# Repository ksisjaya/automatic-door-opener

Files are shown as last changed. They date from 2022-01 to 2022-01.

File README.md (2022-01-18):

# Summary
This project is for the course *ECE 298: Instrumentation and Prototyping*. The objective is to prototype an automatic door opener system using the [STM32F401RE MCU](https://www.st.com/en/microcontrollers-microprocessors/stm32f401re.html). Additional sensors and actuators have also been included to operate the system which is simulated in the [Proteus Design Suite](https://www.labcenter.com/). Labs go through the prototyping design process, beginning with electrical schematics and ending with Gerber plots to fabricate a PCB to host the system.

## Lab 1: Design Requirements
- Define functional, non-functional and constraint requirements
- Choose components and corresponding parameters of operation
- Define connections with the MCU and any internal MCU resources required (e.g. ADC, timers, interrupts, GPIO functions)
- Verification and validation of proper component operation, along with simulations of this
- System level block diagram

## Lab 2: MCU Interfacing
- Determine appropriate hardware interfacing with MCU pins
- Step-down voltage interfaces
- Step-up voltage interfaces
- Analog to digital interfaces
- Motor controller IC interfaces
- Simple simulations and proof-of-concept for these interfaces

## Lab 3: Prototyping
- Connecting all components with the appropriate hardware interfaces to the MCU pins
- Writing embedded software to be run on the MCU (see [Operational Overview.pdf](https://github.com/ksisjaya/automatic-door-opener/blob/main/Lab3/Operational%20Overview.pdf) for an overview of the design)
- Simulate test cases to ensure edge cases have been dealt with

## Lab 4: PCB Design
- Prepare schematics from Lab 3 to be processed into Gerber plots
- Add terminal blocks and rectangular connectors for connections
- Add decoupling capacitors
- Add nets and test points
- Generate a two layer PCB
- Route traces on the PCB
- Add vias where needed
- Generate Gerber plots
- Generate pick and place files for manufacturing
- Generate a bill of materials

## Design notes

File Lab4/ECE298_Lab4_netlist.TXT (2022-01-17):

ISIS SCHEMATIC DESCRIPTION FORMAT 8.0
=====================================
Design:   ECE298_Lab4.pdsprj
Doc. no.: <NONE>
Revision: <NONE>
Author:   <NONE>
Created:  2020-12-15
Modified: 2021-08-05

*PROPERTIES,0    

*MODELDEFS,0    

*PARTLIST,57   
C1,08056D106KAT2A,10u,CODE="Digikey 478-1417-2-ND",EID=35,PACKAGE=CAPC2012X100
C2,08056D106KAT2A,10u,CODE="Digikey 478-1417-2-ND",EID=38,PACKAGE=CAPC2012X100
C3,04022F104Z7B20D,0.1u,CODE="Digikey 311-1047-1-ND",EID=39,PACKAGE=CAPC1005X55
C4,08056D106KAT2A,10u,CODE="Digikey 478-1417-2-ND",EID=32,PACKAGE=CAPC2012X100
C5,04022F104Z7B20D,0.1u,CODE="Digikey 311-1047-1-ND",EID=24,PACKAGE=CAPC1005X55
C6,08056D106KAT2A,10u,CODE="Digikey 478-1417-2-ND",EID=4,PACKAGE=CAPC2012X100
C16,04022F104Z7B20D,0.1u,CODE="Digikey 311-1047-1-ND",EID=4B,PACKAGE=CAPC1005X55
C17,04022F104Z7B20D,0.1u,CODE="Digikey 311-1047-1-ND",EID=D,PACKAGE=CAPC1005X55
CN7,1-534236-9,1-534236-9,CODE=1-534236-9,EID=1,PACKAGE=ECE298_REVTRANS38DIL-1,SUPPLIER=TE_CONNECTIVITY
CN10,1-534236-9,1-534236-9,CODE=1-534236-9,EID=2,PACKAGE=ECE298_REVTRANS38DIL-1,SUPPLIER=TE_CONNECTIVITY
J1,CONN-SIL2,CONN-SIL2,EID=11,PACKAGE=CONN-SIL2
J2,CONN-SIL2,CONN-SIL2,EID=19,PACKAGE=CONN-SIL2
J4,CONN-SIL2,CONN-SIL2,EID=27,PACKAGE=CONN-SIL2
J5,CONN-SIL2,CONN-SIL2,EID=29,PACKAGE=CONN-SIL2
J6,CONN-SIL2,CONN-SIL2,EID=16,PACKAGE=CONN-SIL2
J7,26630301RP2,26630301RP2,CODE="NorComp 26630301RP2",EID=2D,PACKAGE=CON3_1X3_HDR_2663
J8,CONN-SIL4,CONN-SIL4,EID=B,PACKAGE=CONN-SIL4
J10,CONN-SIL7,CONN-SIL7,EID=1F,PACKAGE=CONN-SIL7
J11,CONN-SIL4,CONN-SIL4,EID=13,PACKAGE=CONN-SIL4
J12,TBLOCK-I2,TBLOCK-I2,EID=28,PACKAGE=TBLOCK-I2
J13,PIN,PIN,EID=E,PACKAGE=PIN
J14,PIN,PIN,EID=F,PACKAGE=PIN
J15,PIN,PIN,EID=1D,PACKAGE=PIN
J16,PIN,PIN,EID=22,PACKAGE=PIN
J17,CONN-SIL2,CONN-SIL2,EID=7,PACKAGE=CONN-SIL2
J18,CONN-SIL2,CONN-SIL2,EID=10,PACKAGE=CONN-SIL2
J19,CONN-SIL2,CONN-SIL2,EID=1E,PACKAGE=CONN-SIL2
J20,CONN-SIL2,CONN-SIL2,EID=23,PACKAGE=CONN-SIL2
J21,CONN-SIL2,CONN-SIL2,EID=25,PACKAGE=CONN-SIL2
J31,PIN,PIN,EID=4E,PACKAGE=PIN
J33,PIN,PIN,EID=50,PACKAGE=PIN
J38,PIN,PIN,EID=55,PACKAGE=PIN
J39,PIN,PIN,EID=56,PACKAGE=PIN
Q1,BSS138,BSS138,EID=5,PACKAGE=SOT23,SPICELIB=ZETEX,SPICEMODEL=BSS138
Q2,2N7002,2N7002,EID=2C,L=2.5E-6,PACKAGE=SOT23,SPICELIB=SUPERTEX,SPICEMODEL=2N7002,W=0.5E-2
Q3,2N7002,2N7002,EID=34,L=2.5E-6,PACKAGE=SOT23,SPICELIB=SUPERTEX,SPICEMODEL=2N7002,W=0.5E-2
Q4,2N7002,2N7002,EID=3C,L=2.5E-6,PACKAGE=SOT23,SPICELIB=SUPERTEX,SPICEMODEL=2N7002,W=0.5E-2
Q5,2N7002,2N7002,EID=12,L=2.5E-6,PACKAGE=SOT23,SPICELIB=SUPERTEX,SPICEMODEL=2N7002,W=0.5E-2
Q10,BSS138,BSS138,EID=33,PACKAGE=SOT23,SPICELIB=ZETEX,SPICEMODEL=BSS138
R1,CHIPRES10K,10k,CODE=72-0869,EID=3A,PACKAGE=0805_RES,PRIMTYPE=RESISTOR
R2,CHIPRES10K,10k,CODE=72-0869,EID=17,PACKAGE=0805_RES,PRIMTYPE=RESISTOR
R3,CHIPRES200R,200R,CODE=72-0615,EID=20,PACKAGE=0805_RES,PRIMTYPE=RESISTOR
R4,CHIPRES10K,10k,CODE=72-0869,EID=6,PACKAGE=0805_RES,PRIMTYPE=RESISTOR
R5,CHIPRES200R,200R,CODE=72-0615,EID=2E,PACKAGE=0805_RES,PRIMTYPE=RESISTOR
R6,CHIPRES200R,200R,CODE=72-0615,EID=36,PACKAGE=0805_RES,PRIMTYPE=RESISTOR
R7,CHIPRES200R,200R,CODE=72-0615,EID=3D,PACKAGE=0805_RES,PRIMTYPE=RESISTOR
R8,CHIPRES10K,10k,CODE=72-0869,EID=42,PACKAGE=0805_RES,PRIMTYPE=RESISTOR
R9,CHIPRES10K,10k,CODE=72-0869,EID=3,PACKAGE=0805_RES,PRIMTYPE=RESISTOR
R10,CHIPRES10K,10k,CODE=72-0869,EID=1B,PACKAGE=0805_RES,PRIMTYPE=RESISTOR
R11,CHIPRES10K,10k,CODE=72-0869,EID=8,PACKAGE=0805_RES,PRIMTYPE=RESISTOR
R12,CHIPRES10K,10k,CODE=72-0869,EID=3E,PACKAGE=0805_RES,PRIMTYPE=RESISTOR
R13,CHIPRES10K,10k,CODE=72-0869,EID=21,PACKAGE=0805_RES,PRIMTYPE=RESISTOR
R14,CHIPRES47K,47k,CODE=72-0949,EID=9,PACKAGE=0805_RES,PRIMTYPE=RESISTOR
R15,CHIPRES47K,47k,CODE=72-0949,EID=15,PACKAGE=0805_RES,PRIMTYPE=RESISTOR
R16,CHIPRES91K,91k,CODE=72-0973,EID=A,PACKAGE=0805_RES,PRIMTYPE=RESISTOR
R17,CHIPRES91K,91k,CODE=72-0973,EID=1A,PACKAGE=0805_RES,PRIMTYPE=RESISTOR
U10,DRV8871,DRV8871,EID=14,PACKAGE=SOIC127P600X170-9

*NETLIST,40   
NRST,2,CLASS=SIGNAL
NRST,IT
CN7,PS,14

LEDGO_OUT,3,CLASS=SIGNAL
LEDGO_OUT,LBL
Q5,PS,1
J17,PS,2

PA8,3,CLASS=SIGNAL
PA8,GT
Q5,PS,2
CN10,PS,23

PB14,3,CLASS=SIGNAL
PB14,GT
U10,IP,3
CN10,PS,28

PB13,3,CLASS=SIGNAL
PB13,GT
U10,IP,2
CN10,PS,30

MOTOR_OUT1,4,CLASS=POWER
MOTOR_OUT1,LBL
U10,OP,6
J10,PS,6
J39,PS,1

MOTOR_OUT2,4,CLASS=POWER
MOTOR_OUT2,LBL
U10,OP,8
J10,PS,7
J38,PS,1

MOTOR_ILIM,3,CLASS=POWER
MOTOR_ILIM,LBL
U10,PS,4
R1,PS,1

PA12,3,CLASS=SIGNAL
PA12,GT
J10,PS,2
CN10,PS,12

PB8,3,CLASS=SIGNAL
PB8,GT
J10,PS,3
CN10,PS,3

PB5,4,CLASS=SIGNAL
PB5,GT
R8,PS,1
J18,PS,2
CN10,PS,29

LEDGO_IN,3,CLASS=SIGNAL
LEDGO_IN,LBL
R3,PS,2
J17,PS,1

PC6,4,CLASS=SIGNAL
PC6,GT
J7,PS,2
J31,PS,1
CN10,PS,4

USI_TR,4,CLASS=SIGNAL
USI_TR,LBL
Q10,PS,1
R12,PS,2
J11,PS,3

PC11,3,CLASS=SIGNAL
PC11,GT
Q10,PS,2
CN7,PS,2

USI_ECHO,3,CLASS=SIGNAL
USI_ECHO,LBL
R15,PS,1
J11,PS,4

PB9,4,CLASS=SIGNAL
PB9,GT
R15,PS,2
R17,PS,1
CN10,PS,5

PB6,4,CLASS=SIGNAL
PB6,GT
R9,PS,1
J1,PS,2
CN10,PS,17

PB7,4,CLASS=SIGNAL
PB7,GT
R11,PS,1
J6,PS,1
CN7,PS,21

PC0,4,CLASS=SIGNAL
PC0,GT
R2,PS,1
J21,PS,2
CN7,PS,38

PC1,4,CLASS=SIGNAL
PC1,GT
R10,PS,1
J4,PS,2
CN7,PS,36

PC2,4,CLASS=SIGNAL
PC2,GT
R13,PS,1
J5,PS,2
CN7,PS,35

LEDR_OUT,3,CLASS=SIGNAL
LEDR_OUT,LBL
Q2,PS,1
J2,PS,2

PA10,3,CLASS=SIGNAL
PA10,GT
Q2,PS,2
CN10,PS,33

LEDR_IN,3,CLASS=SIGNAL
LEDR_IN,LBL
R5,PS,2
J2,PS,1

LEDY_OUT,3,CLASS=SIGNAL
LEDY_OUT,LBL
Q3,PS,1
J19,PS,2

PA11,3,CLASS=SIGNAL
PA11,GT
Q3,PS,2
CN10,PS,14

LEDY_IN,3,CLASS=SIGNAL
LEDY_IN,LBL
R6,PS,2
J19,PS,1

LEDGI_OUT,3,CLASS=SIGNAL
LEDGI_OUT,LBL
Q4,PS,1
J20,PS,2

PA9,3,CLASS=SIGNAL
PA9,GT
Q4,PS,2
CN10,PS,21

LEDGI_IN,3,CLASS=SIGNAL
LEDGI_IN,LBL
R7,PS,2
J20,PS,1

USO_TR,4,CLASS=SIGNAL
USO_TR,LBL
Q1,PS,1
R4,PS,2
J8,PS,3

PC9,3,CLASS=SIGNAL
PC9,GT
Q1,PS,2
CN10,PS,1

USO_ECHO,4,CLASS=SIGNAL
USO_ECHO,LBL
R14,PS,1
J8,PS,4
J33,PS,1

PC10,4,CLASS=SIGNAL
PC10,GT
R14,PS,2
R16,PS,1
CN7,PS,1

{NC},47
CN10,PS,2
CN10,PS,6
CN10,PS,11
CN10,PS,13
CN10,PS,15
CN10,PS,16
CN10,PS,19
CN10,PS,22
CN10,PS,24
CN10,PS,25
CN10,PS,26
CN10,PS,27
CN10,PS,34
CN7,PS,34
CN7,PS,37
CN7,PS,32
CN7,PS,30
CN7,PS,28
CN7,PS,3
J10,PS,1
CN10,PS,8
CN10,PS,7
CN10,PS,38
CN10,PS,37
CN10,PS,36
CN10,PS,35
CN10,PS,31
CN10,PS,18
CN10,PS,10
CN7,PS,9
CN7,PS,7
CN7,PS,6
CN7,PS,5
CN7,PS,4
CN7,PS,33
CN7,PS,31
CN7,PS,29
CN7,PS,27
CN7,PS,26
CN7,PS,25
CN7,PS,24
CN7,PS,23
CN7,PS,17
CN7,PS,15
CN7,PS,13
CN7,PS,11
CN7,PS,10

+3.3V,12,CLASS=POWER
+3.3V,PR
C6,PS,1
J5,PS,1
J4,PS,1
J21,PS,1
J6,PS,2
J1,PS,1
C1,PS,1
J15,PS,1
J18,PS,1
CN7,PS,16
CN7,PS,12

+5.0V,17,CLASS=POWER
+5.0V,PR
R4,PS,1
C17,PS,1
J8,PS,1
R7,PS,1
R6,PS,1
R5,PS,1
C2,PS,1
J14,PS,1
R12,PS,1
C16,PS,1
J11,PS,1
J10,PS,5
J7,PS,1
C5,PS,1
R3,PS,1
CN7,PS,18

+12.0V,6,CLASS=POWER
+12.0V,PR
J12,PS,1
C4,PS,1
J16,PS,1
U10,PP,5
C3,PS,1

GND,40,CLASS=POWER
GND,PR
C17,PS,2
Q1,PS,3
R16,PS,2
J8,PS,2
Q4,PS,3
Q3,PS,3
Q2,PS,3
R13,PS,2
R10,PS,2
R2,PS,2
R11,PS,2
R9,PS,2
C16,PS,2
C3,PS,2
Q10,PS,3
R17,PS,2
J11,PS,2
J12,PS,2
C4,PS,2
J13,PS,1
C1,PS,2
C6,PS,2
C2,PS,2
J10,PS,4
J7,PS,3
C5,PS,2
R8,PS,2
U10,PP,7
U10,PP,1
U10,PP,9
R1,PS,2
Q5,PS,3
CN10,PS,9
CN10,PS,32
CN10,PS,20
CN7,PS,8
CN7,PS,22
CN7,PS,20
CN7,PS,19

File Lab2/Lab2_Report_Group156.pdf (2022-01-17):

# Lab 2 – Feasibility Model Phase 2

ECE 298 – S2021

Lab Section: | 1215-ECE.298.041.8.LAB | Group: | 156

## DC Motor

### Summary

Item | Description
Purpose | The motor will open and close the door.
Device physical domain and range | As described in the device properties window, the motor has a zero load rotations per minute (RPM) of 360 and it runs at 24 pulses per revolution. No maximum rotations per minute is given in the device data sheet, but on testing using a 12 Volt source with a motor driver integrated circuit (IC) as shown below, the motor turns at a maximum of 176 RPM. Note that this is slightly lower than the previously tested maximum (from Lab 1) of 180 RPM, when it was directly attached to a 12 V source instead of a driver.
Device type chosen | Brushed DC Motor
Proteus Library component name | ECE298_DCMOTOR_ENCODER
Device input / output properties | The motor has two terminal inputs, in which an analog voltage is applied across. The sign (positive or negative) of the potential difference across the motor determines its direction. Note that the motor outputs (i.e. pins Q1, Q2, and IDX) are described in the 'Motor Encoder' table. Additionally, a motor driver IC (DRV8871) will be used, which accepts two digital inputs (IN1 and IN2), a 12 V source at the VM pin, and outputs an analog signal (OUT1 and OUT2) to the motor.
Device input / output range | The motor accepts voltages from 0V to 12V. Note that if accepting a pulse-width modulated (PWM) signal, the motor driver accepts a maximum logic input PWM frequency of 200 kHz (Table 6.3 of the device datasheet), while the microcontroller unit (MCU) can output a maximum PWM frequency of 42 MHz (Table 58 of the MCU datasheet). Therefore, the PWM frequency in the sub-system has a maximum of 200 kHz.
MCU connectivity details | To control the motor speed, a digital PWM output from the MCU will be required.
Device/MCU interfacing details | The MCU digital PWM output signals will be connected to the input pins (IN1 and IN2) of the DRV8871 motor driver IC. This driver will be connected to a 12 V source at the VM pin that will power the motor, thus acting as a digital to analog converter.

Lab 2 – Feasibility Model Phase 2

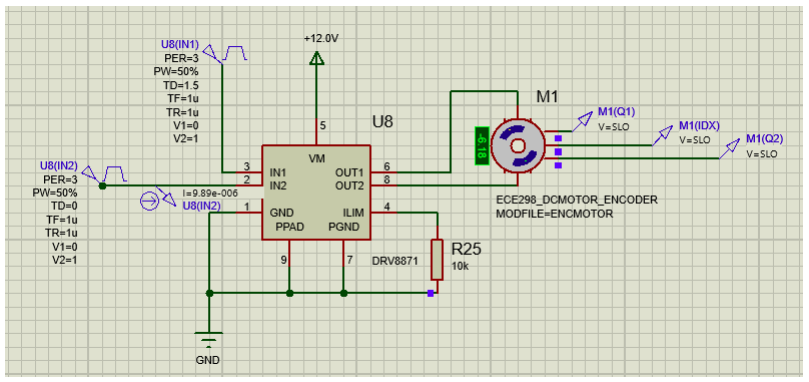
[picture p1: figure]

ECE 298 S2021Page 2 of 21

### Schematics and Simulations

Several aspects of the DC motor will be tested when driven by the interface as described above.

Figure 1 shows the schematic to test for the motor going in both directions using the motor driver interface. To simulate the outputs of the MCU digital pins, square waves with a low of 0V and high of 3.3V are outputted into IN1 and IN2. The waves have a pulse width of 50% and period of 3 seconds. It should be noted that IN1 begins at 1.5 seconds, shifting it by half a period with respect to IN2. This will simulate the MCU driving the motor to go in different directions (in this case, it will oscillate between clockwise and counterclockwise). Also note that the motor driver VM pin is connected to a 12V source; the OUT1 and OUT2 pins are connected to the motor's two terminals; the ILIM pin has a 10kOhm resistor to ground; and the PGND, PPAD and GND pins are all grounded.

Fig. 1: Motor direction testing schematic

Figure 2 shows the outputs of Q1, Q2, and IDX of the motor. The motor is set to 24 pulses per revolution, indicated by the pulses created by IDX. Likewise, as with Lab 1, the direction of the motor can be detected by the rising edges of Q1 and Q2. At 1.5 seconds, the motor is at an inflection point in turning its direction. This is reflected by the longer pulses of Q1 and Q2, indicating a slowing down of motor revolutions. After 1.5 seconds, we can see that the rising edge relationship between Q1 and Q2 has flipped, thus indicating that the motor is now rotating in the opposite direction. This pattern is repeated at 3 seconds. Thus, given this interface can drive the motor in either direction, it will be suitable.

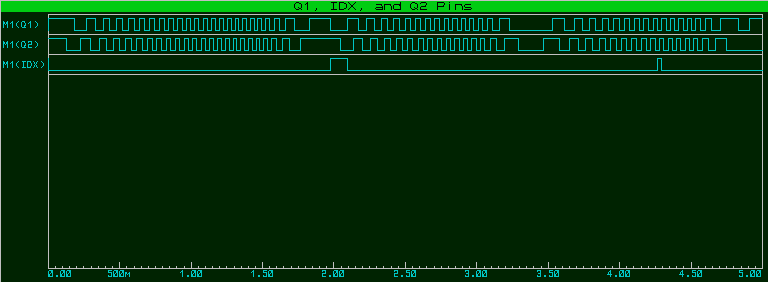
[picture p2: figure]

Fig. 2: Motor direction testing results

Figure 3 shows the schematic to test full-power in-rush current of the motor, as well as the current pulled from the MCU output at full-power. In this test, IN1 is given a constant 3.3V to represent an MCU digital output at a strong high, and IN2 is given a constant 0V to represent an MCU digital output at a strong low. Doing so provides the full extent of what the MCU can output, thus providing full power to the motor driver and therefore motor.

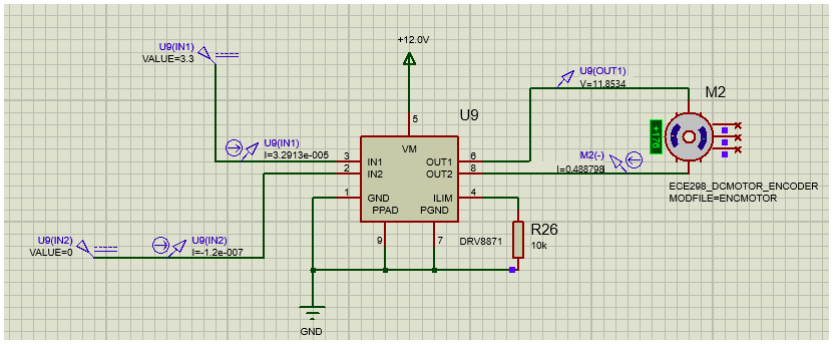
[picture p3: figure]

Fig. 3: Full power in-rush testing schematic

First, it would be useful to know if the interface draws a current within the limits of the MCU pins. Figure 4 shows the current drawn from the MCU outputs at IN1 and IN2. For U9(IN1), for which the maximum digital output from the MCU is supplied, the current remains constant at around 33µA. For U9(IN2), for which the digital output is a strong low, the current remains constant at near 0A. Therefore, the current drawn from the MCU digital output pins can be anywhere from 0A to 33µA when connected to this motor driver interface. This is much lower than the limit of 25mA per pin, making it a suitable interface.

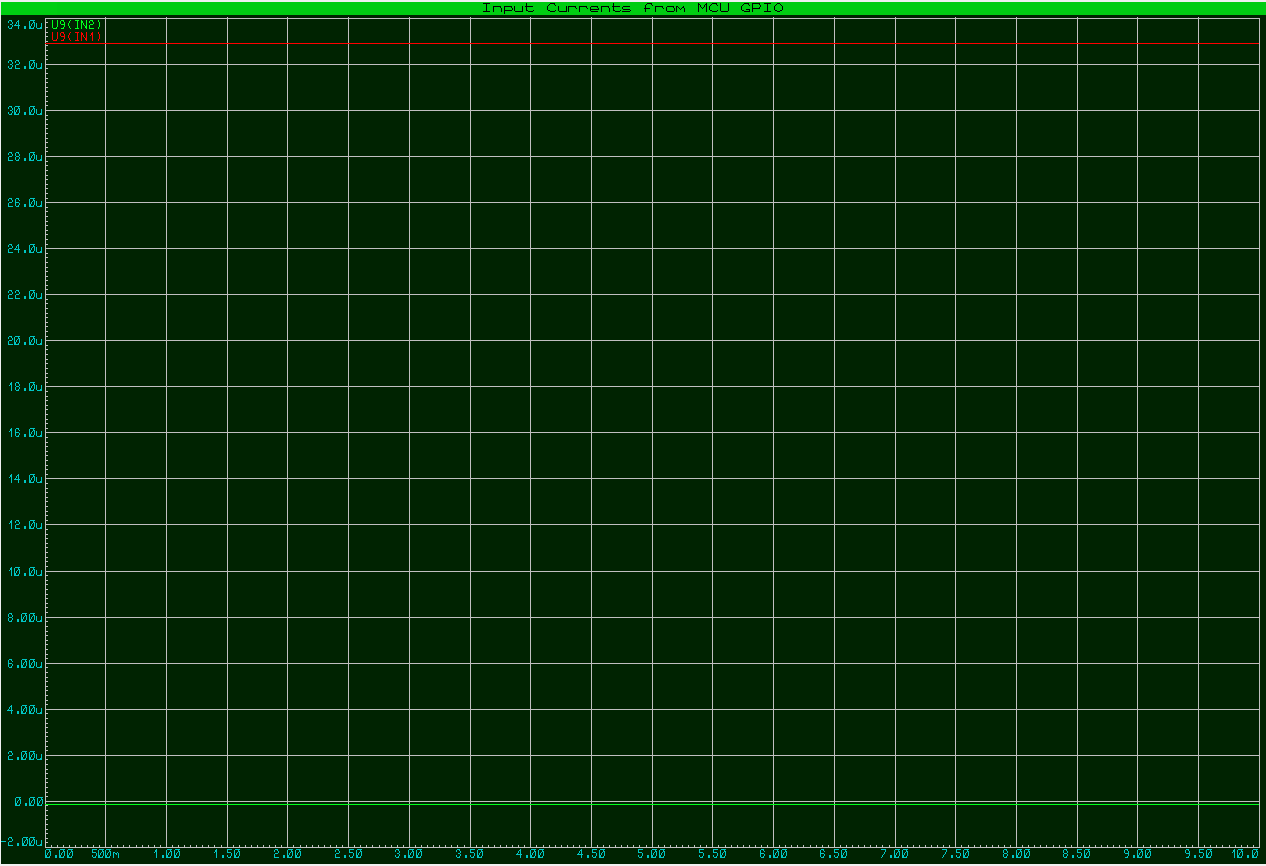
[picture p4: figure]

Fig. 4: Full power in-rush input currents to the motor driver

Figure 5 shows the full-power in-rush motor current and voltage. The voltage remains at a constant 12V, as the motor draws it from the source connected to the VM pin. The current spikes to around 952mA and stabilizes to around 500mA. Table 6.1 of the motor driver IC datasheet shows that the absolute maximum rating for the output current (at 100% duty cycle) is 3.5A. As such, the 952mA full-power in-rush current is tolerable and will not pose any major danger to damaging the IC. Therefore, this interface will be suitable in terms of handling the full power in-rush current.

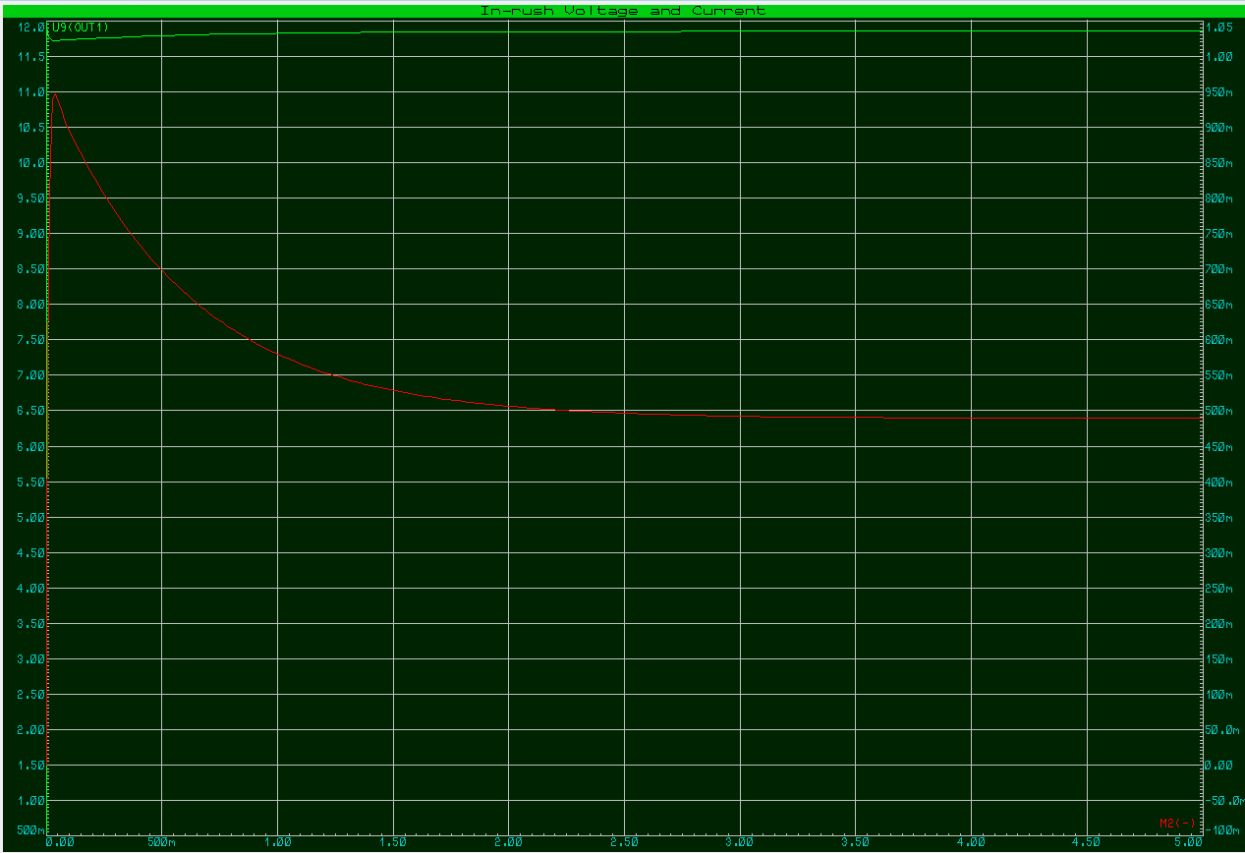
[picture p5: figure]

Fig. 5: Full power in-rush motor current and voltage

Figure 6 shows the schematic to test the motor voltage and current at varying inputs. As with the previous test, IN2 is set to 0V. However, this test sets IN1 to varying inputs of voltages (0V, 1V, 2V, 3V) to see what the interface response would be if the MCU pin output a weak high or weak low. Note that the IN1 voltages go from 0V to 3V and then down to 0V again. This is to test what the IC response would be in both directions.

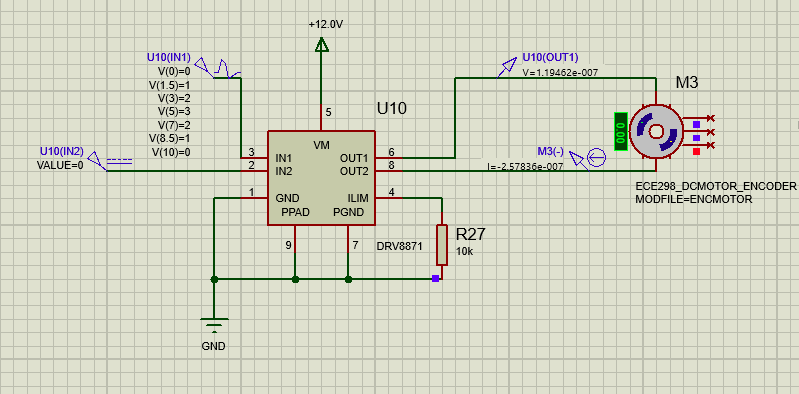
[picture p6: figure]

Fig. 6: Motor voltage and current testing schematic

Figure 7 shows the voltage and current of the motor. The voltages across the motor respond in a step-like manner, where it jumps from one value to the next. This is because the motor is no longer attached directly to the input, but rather it is being sourced by the 12V at VM. IN1 and IN2 only determines the response of the H-bridge as shown in section 7.2 of the device datasheet, which in turn determines the voltage supplied to the motor. One can see that the voltage at its maximum reaches 12V. With every step up of voltage, the current responds as though it is an in-rush current, shooting upwards and then decaying. With every step down of voltage, the current responds as though it is an out-rush current, shooting downwards and then exponentially growing. These are determined by the time constants made up of the internal resistance of the motor and any parasitic capacitances that exist. Again, the peak current only reaches around 800mA, which is far below the motor’s maximum limit (3.5A) as described in Table 6.1 of the datasheet. Therefore, the performance of this interface is within limits and is suitable.

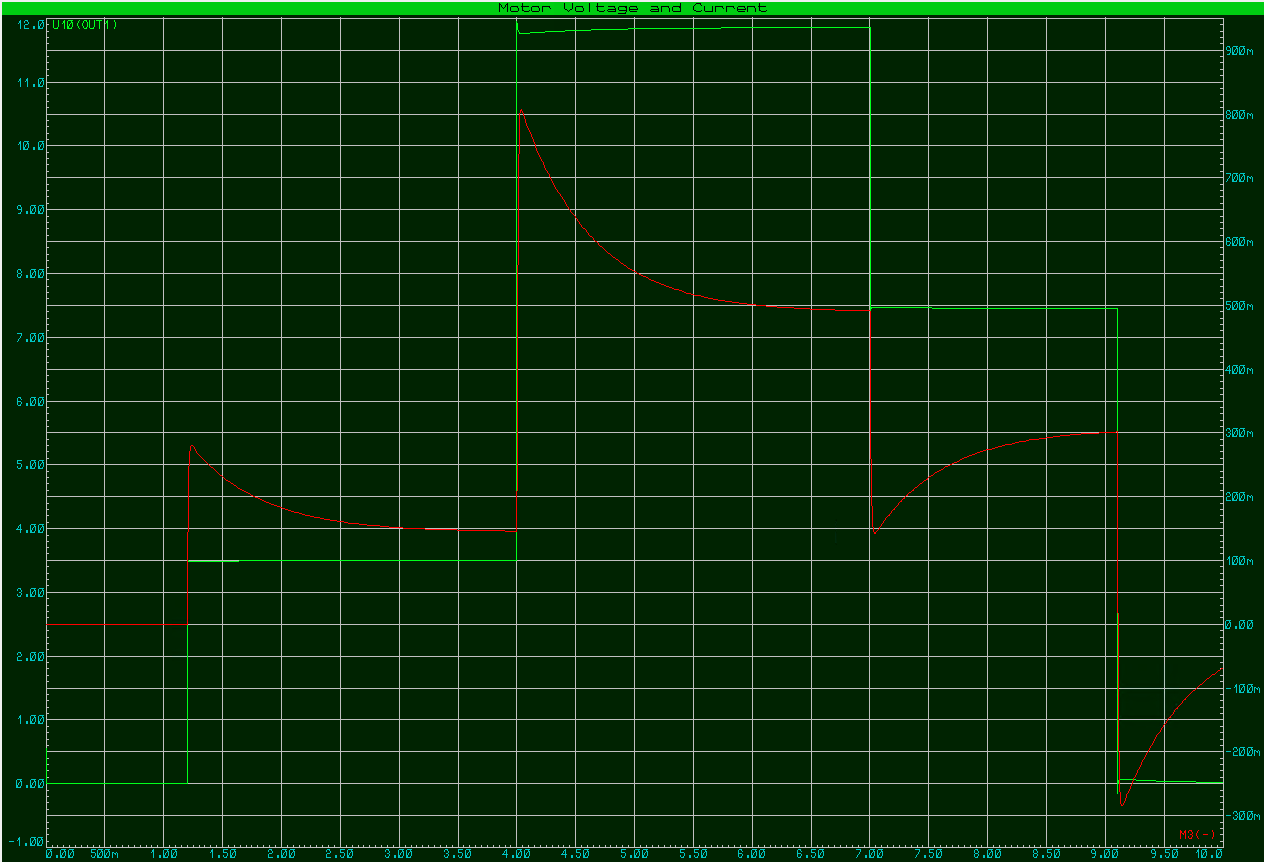
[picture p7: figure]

Fig. 7: Motor voltage and current testing results (note: y-axis scales for voltage and current do not align)

Figure 8 shows the schematic to test the motor interface under a PWM input. The PWM input is given by the PWM_input_testing.txt file which has a PWM signal with a low of 0V and high of 3.3V. As described in the device datasheet, the motor driver can take in a PWM input through IN1 and IN2, and the driver will be able to output another PWM signal to the motor. For this test, IN2 was set to 0V and IN1 had the PWM input. This corresponds to the description in the data sheet on how to use the motor driver to drive a PWM signal to the motor.

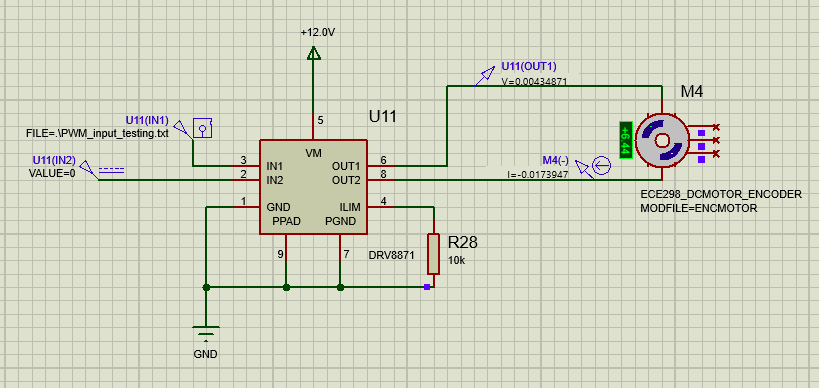
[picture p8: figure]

Fig. 8: PWM input testing schematic

Figure 9 shows the current and voltage across the motor as the PWM signal is being input. The voltage oscillates between 0V and 12V, as is expected (given that the VM pin is connected to a 12V source), and the current responds as an in-rush current, shooting up then decaying. During the PWM signal with a higher frequency, the current shoots up and down in several 'steps'. The rather quick time constant means that the current decays very quickly, resulting in larger oscillations. This can be seen by the first 'step' of current from 500ms to 700ms, where the current fluctuates between 200mA to 500mA. It should be noted that 7.4.1 and 7.4.2 of the device datasheet indicates that the motor driver can operate a PWM signal with or without current regulation. As such, it would be possible to be safer and more precise in terms of current behavior. Also note that Table 6.3 of the datasheet shows the maximum PWM frequency to be 200kHz. This is the bottleneck if also considering the MCU's maximum PWM frequency of 42 MHz. Either way, the RPM measurements of the PWM signal from the text file (which has a frequency much less than 200kHz) is high enough to provide for our needs. As such, this interface will be suitable with a PWM input. We just need to decide the proper duty cycles and frequencies of the PWM signal for our purposes.

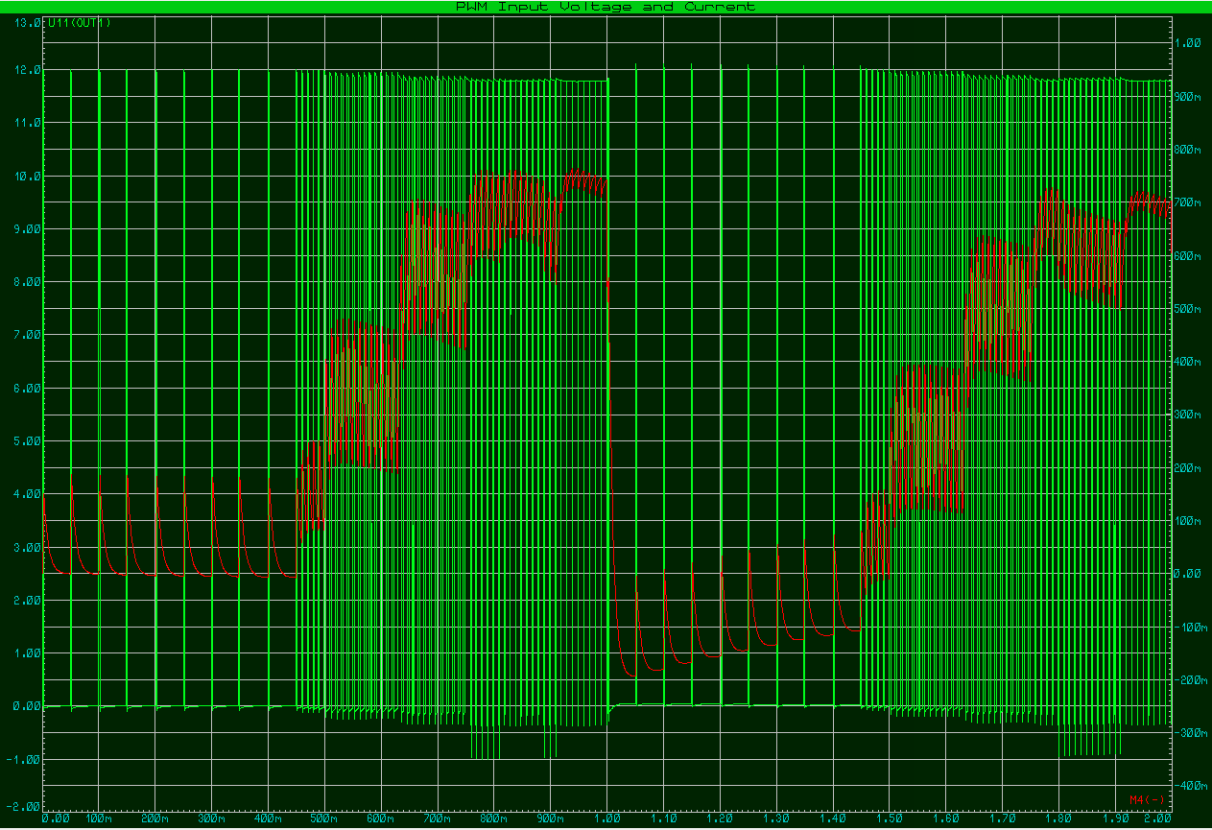
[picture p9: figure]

Fig. 9: PWM input testing results

## Light Emitting Diode (LED)

### Summary

Item | Description
Purpose | To indicate to the user the current state of the automatic door system. A red LED indicates the door in motion, a yellow LED indicates the door has collided with an object, and a green LED indicates an object is within the inside and outside proximity ranges.
Device physical domain and range | The light intensity of the LED (determined when the specific LED is chosen later) and the color of the LED (green, red, and yellow).
Device type chosen | LED
Proteus Library component name | LED-RED, LED-GREEN, LED-YELLOW
Device input / output properties | The LED has two terminals, which when an analog is applied across, will produce a current, lighting the LED. For all three components, the forward voltage at 20 mA is 2.2 V, the full drive current is 10 mA, and the minimum on-time to light the LED is 10ms.
Device input / output range | The breakdown voltage of the LEDs is 4 V, meaning that there should not be a voltage applied in the reverse direction of the diode more than 4 V. Otherwise, the LED will be damaged.

MCU connectivity details | The MCU will output a digital signal through the correct pin that is connected to the corresponding LED. Note that it is assumed that only one LED color can be turned on at a time.
Device/MCU interfacing details | The MCU pin will output a digital signal to the gate terminal of an n-channel MOSFET (2N7002). The MOSFET will act as a switch for the LED, which is connected via the drain terminal to a 5 V analog source with a pull-up resistor of 145 Ohms. The source terminal will be grounded. A digital high signal (3.3 V) applied by the MCU digital output is enough to allow current to 'turn on' the transistor, resulting in an analog input into the LED. As such, the interface acts as a digital to analog converter.

### Schematics and Simulations

Figure 10 shows the schematic for LED testing. To simulate an MCU digital output, a square wave with a low of 0V and high of 3.3V are outputted into the gate terminal of the n-channel MOSFET. The wave has a frequency of 0.5Hz, and a pulse-width of 50%. The LED is attached to the drain terminal of the MOSFET with a pull-up resistor (145 Ohm) and 5V source, and the source terminal of the MOSFET is grounded. Note that the square waves begin at 0s, 0.3s, and 0.6s for the green, red, and yellow LEDs respectively. This is to make the current measurement easier to read. But also note, that this would mean the LEDs do not turn on at the same time in the simulation.

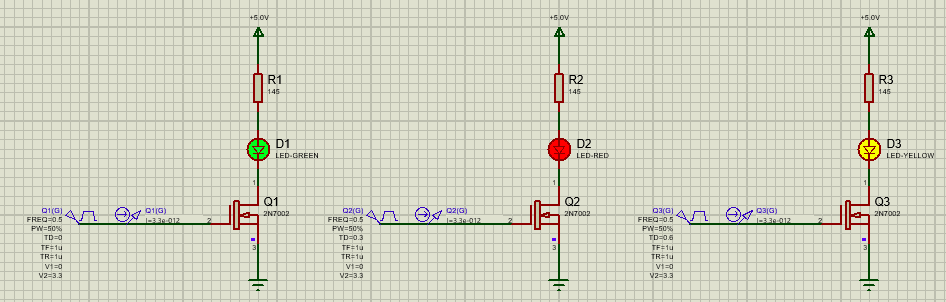
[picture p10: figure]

Fig. 10: LED interface testing schematic

Figure 11 shows the currents being drawn from the MCU pins into the interface. The maximum current being pulled from any of the three LEDs at Q1, Q2, and Q3 respectively, is around 560µA. Likewise, the minimum current being pulled from any of the three LEDS does not go below -250µA. As such, the range of operation for this interface is from -250µA to 560µA. This is far lower than the limit given in the MCU datasheet of +/-25mA per pin. Given there are 4 total LEDs in this project, the worst-case scenario would give an aggregate current of 2.24mA (i.e. all LEDs are on), which is far lower than the aggregate limit of 120mA. Also, most importantly, the LEDs turn on when the signal is high, and off when the signal is low. As such, given all these considerations, this interface will be suitable.

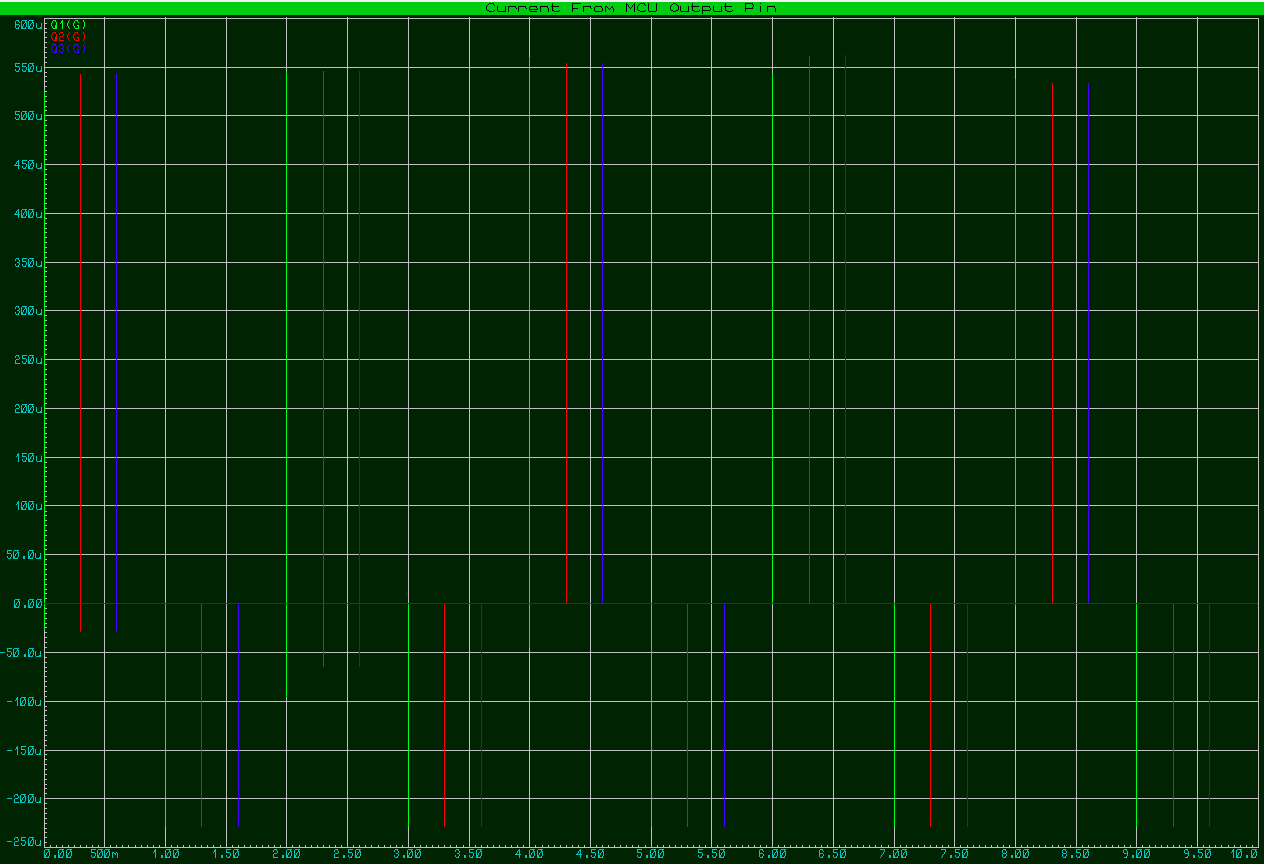
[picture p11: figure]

Fig. 11: LED interface testing results

## Liquid Crystal Display (LCD)

### Summary

Item | Description
Purpose | The LCD displays an alphanumeric string indicating the current mode of operation of the door.
Device physical domain and range | The alphanumeric string to be output to the LCD.
Device type chosen | LCD
Proteus Library component name | LM016L
Device input / output properties | The LCD has eight parallel data bus lines (D0 to D7) that correspond to the byte mapping of the ASCII characters to output. There is also an enable signal pin (E), a read-write pin (R/W), a register selector pin (RS), and the power supply pins (VDD, VSS, VEE).
Device input / output range | The LCD takes +5V digital inputs at 1 to 10 mA (section II.A of the device datasheet). The datasheet in Proteus does not show a minimum input high or a maximum input low, but the Hitachi datasheet (found online) shows a minimum input high voltage of 2.2 V and maximum input low voltage of 0.6 V (Hitachi). (https://datasheetspdf.com/pdf-file/1462370/Hitachi/LM016L/1)

MCU connectivity details | The MCU will output digital signals for the following pins on the LCD: enable (E), register select (RS), read/write (R/W), data (for now it is D7 to D4, but in the future this may include all eight pins).
Device/MCU interfacing details | The MCU digital output will be 3.3V, while the LCD accepts only 5V digital inputs. As such, a digital-to-digital unidirectional step- up voltage interface will be used to bring up the voltage to 5V. This involves inputting the MCU signal into the gate of an n- channel MOSFET, with the source grounded, and the drain connected to a pull-up resistor of 100kOhm with a 5V source. The output will be taken from the drain. But this output will be inverted. As such, an extra inverter is added to re-invert the signal to match the input signal. This step-up voltage interface will be implemented for each LCD pin being used (E, RS, RW, Data pins)..

### Schematics and Simulations

Figure 11 shows the schematic for testing the LCD using the interface. It should be noted that a pattern generator was used. However, this pattern generator only output 5V digital signals. As such, that output first needed to be stepped down to 3.3V to mimic the digital outputs coming from the MCU pins. This circuitry is shown in Figure 12, where all the needed pins from the pattern generator are pulled down using a voltage divider with two resistors of 47kOhm and 91kOhm. The pattern generator and the step down digital to digital voltage dividers can be thought of as the MCU internals, which would then output the appropriate 3.3V digital signals to the external interface, shown in Figure 13. The LCD also takes in only 5V digital signals. As such, the 3.3V outputs from the MCU need to be stepped-up using an n-channel MOSFET with a pull up resistor of 100kOhm and a 5V source. The MCU output is connected to the gate of the MOSFET, the pull up resistor to the drain, and ground to the source. However, this stepped-up voltage will be inverted due to the n-channel MOSFET. So, an extra inverter is required to re-invert the output signal, so it matches the input signal. Note that the E, R/W, and RS pins are connected, alongside the data bus line (which for now are just D7 to D4). As with Lab 1, the pattern is set to output the team number '156'.

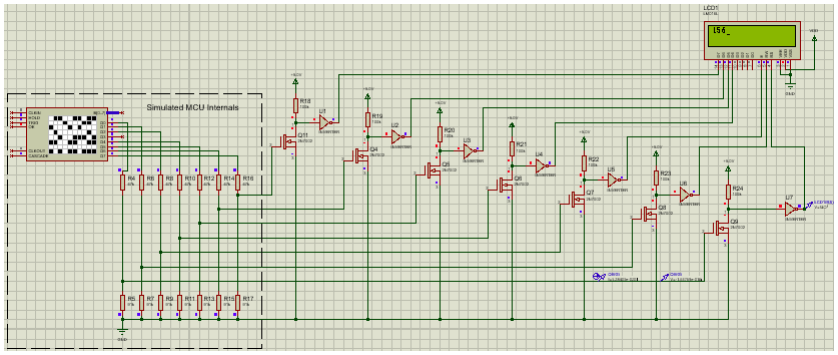
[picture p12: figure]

Fig. 11: LCD interface testing schematic

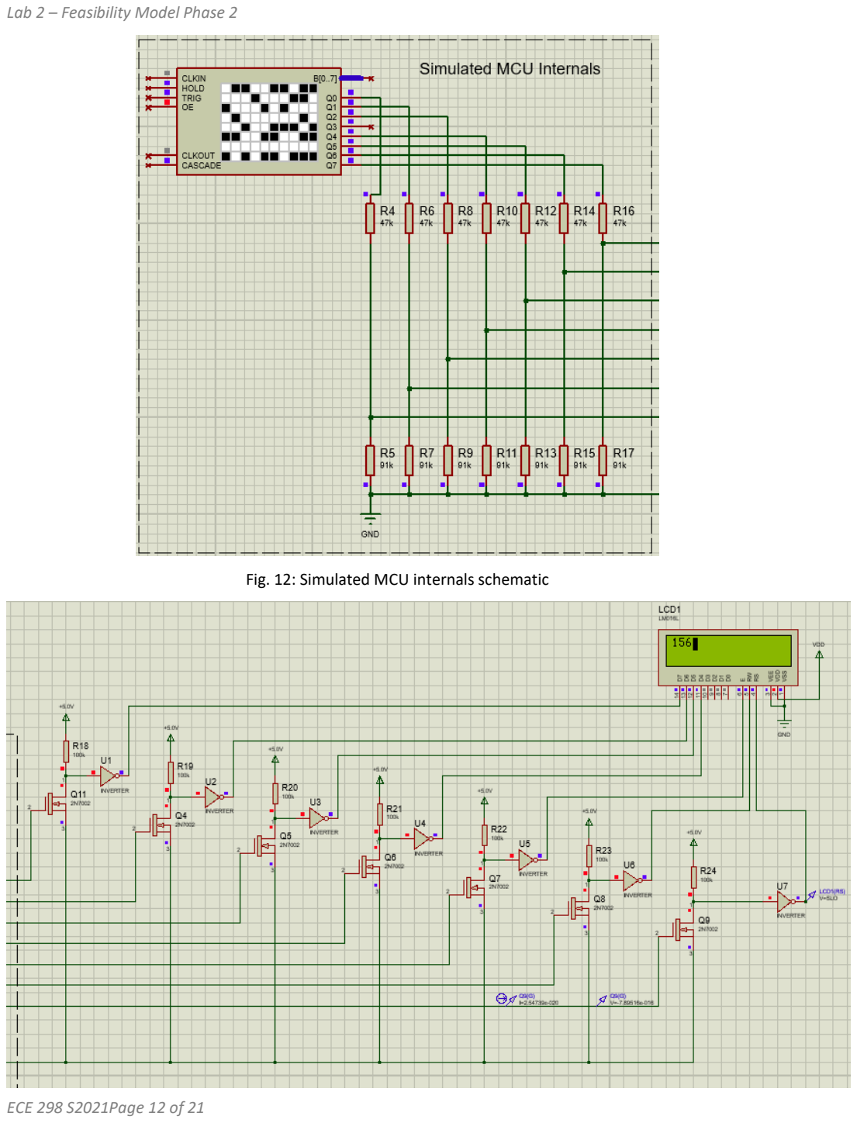
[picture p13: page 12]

Fig. 12: Simulated MCU internals schematic

Fig. 13: LCD external interface schematic

Figure 14 shows the input current, input voltage at Q9 (i.e. one of the MCU digital outputs). The figure also includes the output of the interface at LCD1(RS). First, the input current to the interface reaches a maximum of around 110µA (at 4.5 seconds), and a minimum of around -110µA (at 8.5 seconds). These current spikes coincide with transitions from a strong low to a strong high and vice versa. Either way, this tells us that the interface will draw a range of current from -110µA to 110µA, which is far below the stated MCU limit per pin of +/- 25mA. Assuming that all LCD pins are being outputted to at the same time, the aggregate current drawn from the MCU pins will be 110µA x 11, which is 1.21mA. This is also far below the stated aggregate limit on the MCU pins of 120mA. Therefore, this interface will be appropriate for the current limits. Also, it can be seen that as the input voltage is a strong low (i.e. 0V), so is the output voltage. When the input voltage Q9(G) is a strong high (3.3V from the MCU), the output voltage LCD1(RS) is a strong high of 5V for the LCD. This indicates that the step-up interface works, and this is further shown by the LCD correctly displaying '156'. Therefore, this interface will be suitable.

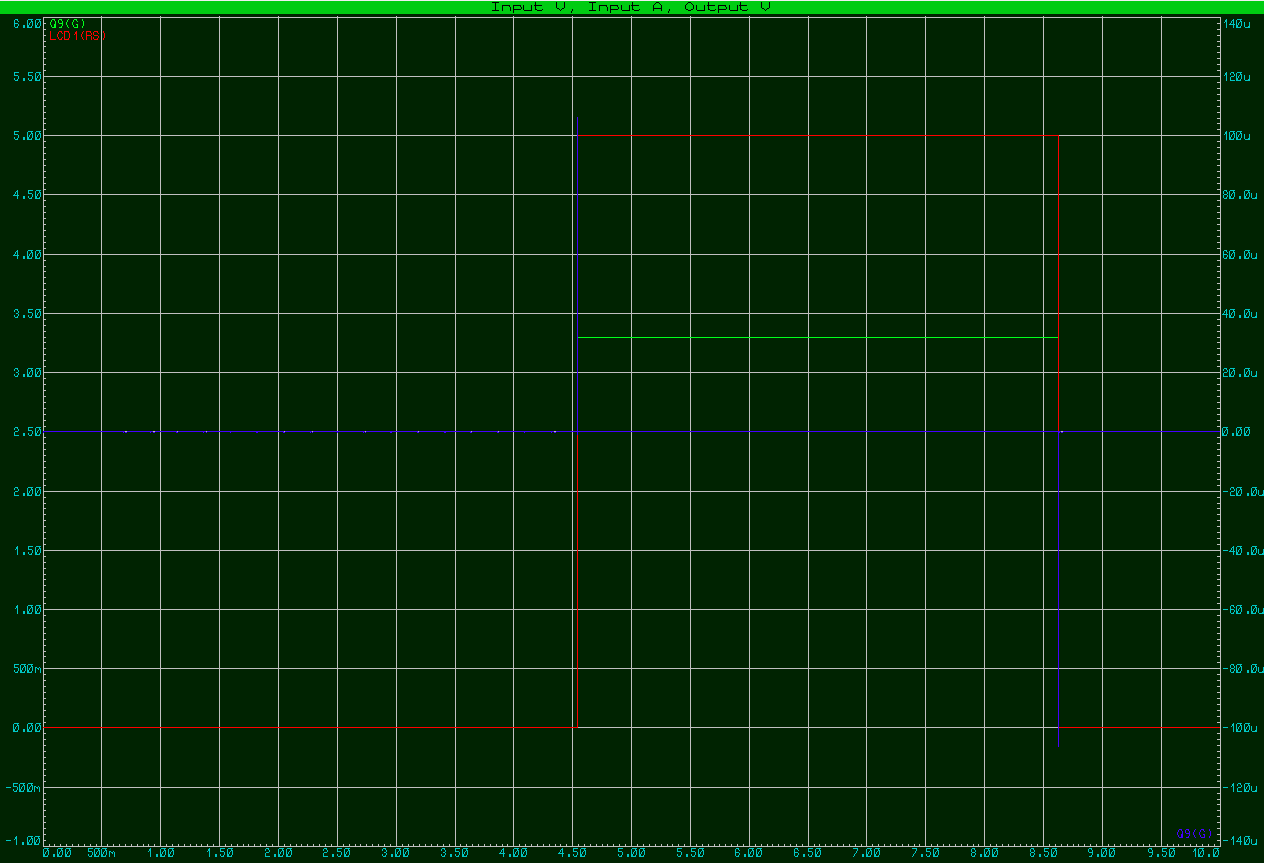
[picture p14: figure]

Fig. 14: LCD interface testing results

## Ultrasonic Ranger Module

### Summary

Item | Description
Purpose | Detects when an object is within a certain distance of the sensor so the door can automatically open.
Device physical domain and range | The module senses objects within 2cm to 4m in a range of 15 degrees.
Device type chosen | The chosen sensor is an ultrasonic proximity sensor
Proteus Library component name | HCSR04
Device input / output properties | The device has four digital input/output pins. One for source voltage and ground. The other two correspond to the input trigger TTL pulse and the time-varying echo pulse (depends time taken by pulse to leave and return). The input and output are push-pull since they can only be two values, strong 0 or strong 1.
Device input / output range | The device has a working voltage of 5V. VOH, min = 2.7V. VOL, max = 0.4V. VIH, max = 2V. VIL, min = 0.8V. The input trigger pulse must have a width of 10us and cannot be transmitted again until the echo has returned or timed out (60ms). The output signal will have a 8* 25us delay since it must wait for the sonic burst to output from the module. The output signal corresponds to the distance measured to an object and could range from around 150 us to 25ms or up to 38ms if nothing is detected.
MCU connectivity details | A digital input pin and a digital output pin will be needed for the trigger and echo pins.
Device/MCU interfacing details | Input: (D/D) The input will need an N-channel MOSFET with a pullup up resistor with an inverted signal to increase the signal. Output: (D/D) The output will need a voltage divider to scale down the signal.

### Schematics and Simulations

Figure 15 shows the schematic for testing MCU input and output to the ultrasonic ranger module. The Q1 signal generator simulates the MCU output and the Pi terminal represents the input to the MCU. Since the N-channel MOSFET inverts the signal, Q1 must start at a constant high signal of 3.3V and generate a 10us pulse of 0V. In Figure 16, you can see that’s what it does and the MOSFET correctly inverts and adjusts the signal to a 5V pulse of 10us into the trigger.

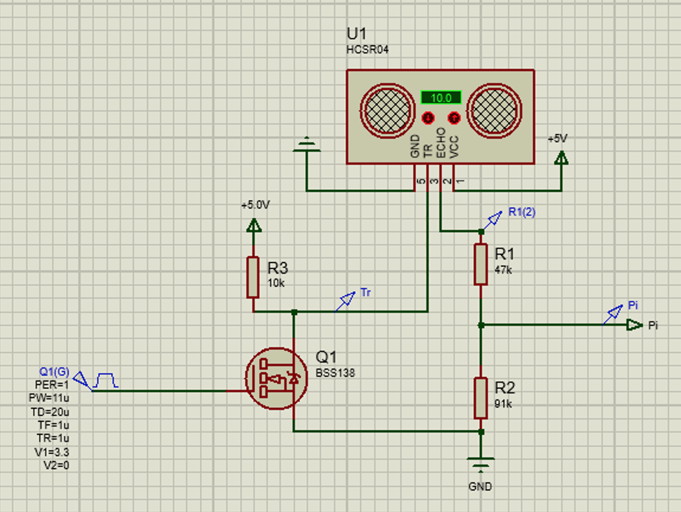
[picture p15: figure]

Fig. 15: Ultrasonic Ranger Module Interface Circuit

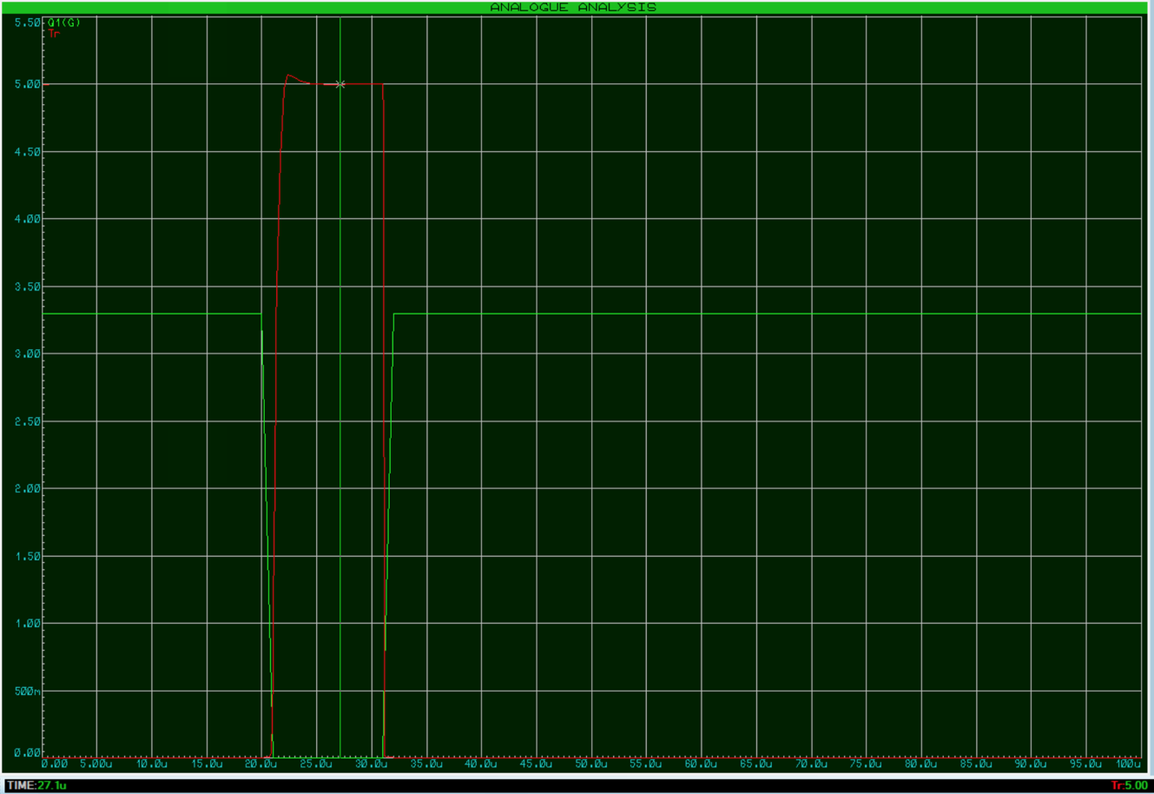
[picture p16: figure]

Fig. 16: Analog Analysis of the simulated MCU output (Q1) and the adjusted trigger input (Tr).

In Figure 17, the voltages on the ECHO line of the ranger are shown in the analog analysis as well. The signal produced straight out of the ranger module gives a varying pulse of 5V. The duration of the pulse depends on the distance of the object sensed and is not currently relevant. After adding a voltage divider, the signal is correctly reduced to 3.3 V without any change other than the magnitude, asserting that the MCU will obtain an accurate reading of the device.

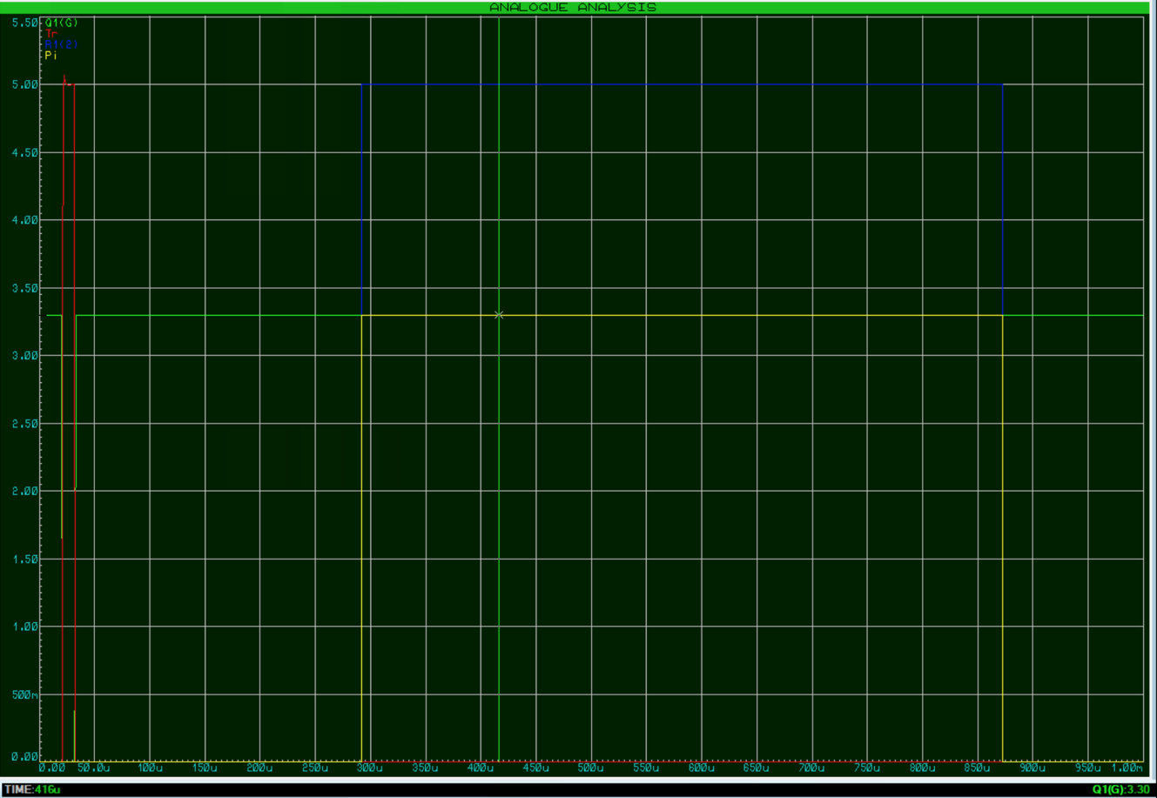
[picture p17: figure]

Fig. 17: Analog Analysis of all the voltages

## DC Motor Encoder

### Summary

Item | Description
Purpose | Senses and monitors speed and rotational direction of the door motor.
Device physical domain and range | The encoder will detect up to the motor’s maximum speed and whether it is turning clockwise or anticlockwise
Device type chosen | A position encoder attached to the shaft of a DC motor.
Proteus Library component name | ECE298_DCMOTOR_ENCODER
Device input / output properties | The encoder outputs three digital signals that are all push-pull. Two outputs must be read together to determine the rotational direction and speed of the motor. The third signal generated can also be read to determine the speed of the motor. The frequencies of the signals depend on the speed of the motor.
Device input / output range | The device has a working voltage of 5V. VOH, min = 2.7V. VOL, max = 0.4 V.
MCU connectivity details | Three digital input pins will be needed to read the signals of the encoder.
Device/MCU interfacing details | Output: (D/D), The outputs will need voltage dividers to scale down the signal.

### Schematics and Simulations

Figure 18 shows the schematic for testing the DC motor encoder. The probes labelled R7(2), R8(1), and R6(2) represents the input pins into the MCU. Since the max voltage of the output from the encoder is greater than what is accepted into the MCU, three voltage dividers will be needed to reduce the signal. A generic 1V DC generator is inputted into the motor to run it, since the encoder depends on the motor to work.

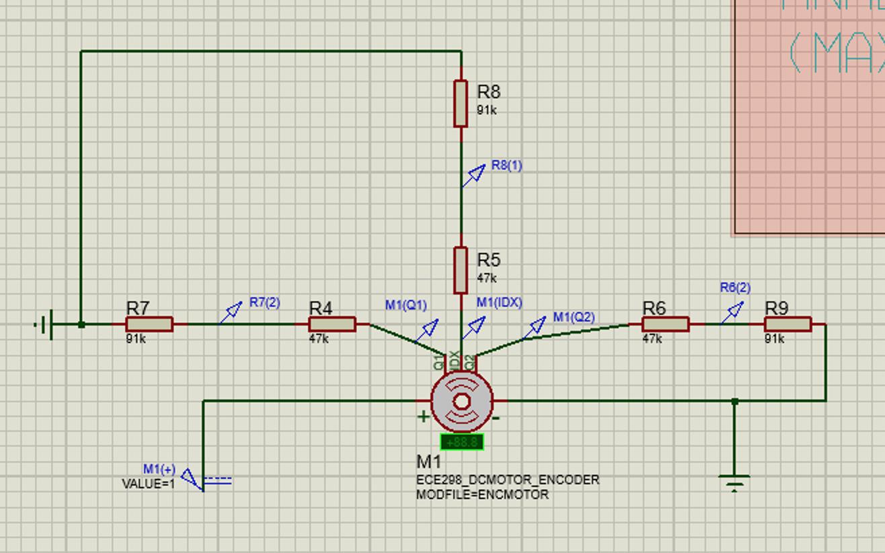
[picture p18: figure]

Fig. 18: DC Motor Encoder Interface Circuit

Figure 19 shows the three outputs of the encoder. All three signals have a high of 5V which is too high for the MCU to read. The pulses of the signal are dependent on the rotational speed and direction of the motor and are not relevant currently. Using digital analysis they can be more accurately read and deciphered but that is not necessary for only interfacing testing with the MCU.

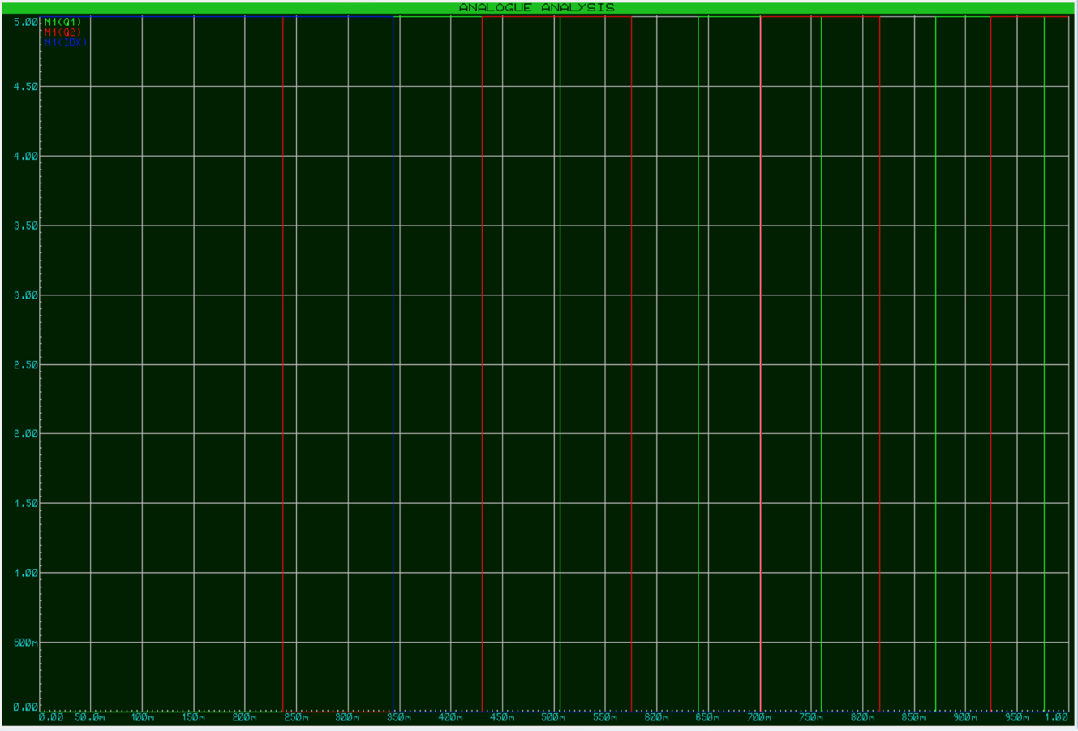
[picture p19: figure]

Fig. 19: Analog Analysis of the Outputs of the Encoder

In figure 20, the analog analysis shows the readings of the probes, simulating the signal into the MCU. The signal has been reduced to 3.3V which is what we need. Also, when comparing with Figure 19, there is no difference between the output of the encoder and the input into the MCU other than the magnitude of the signal which is important since we need to preserve the information transmitted by the encoder.

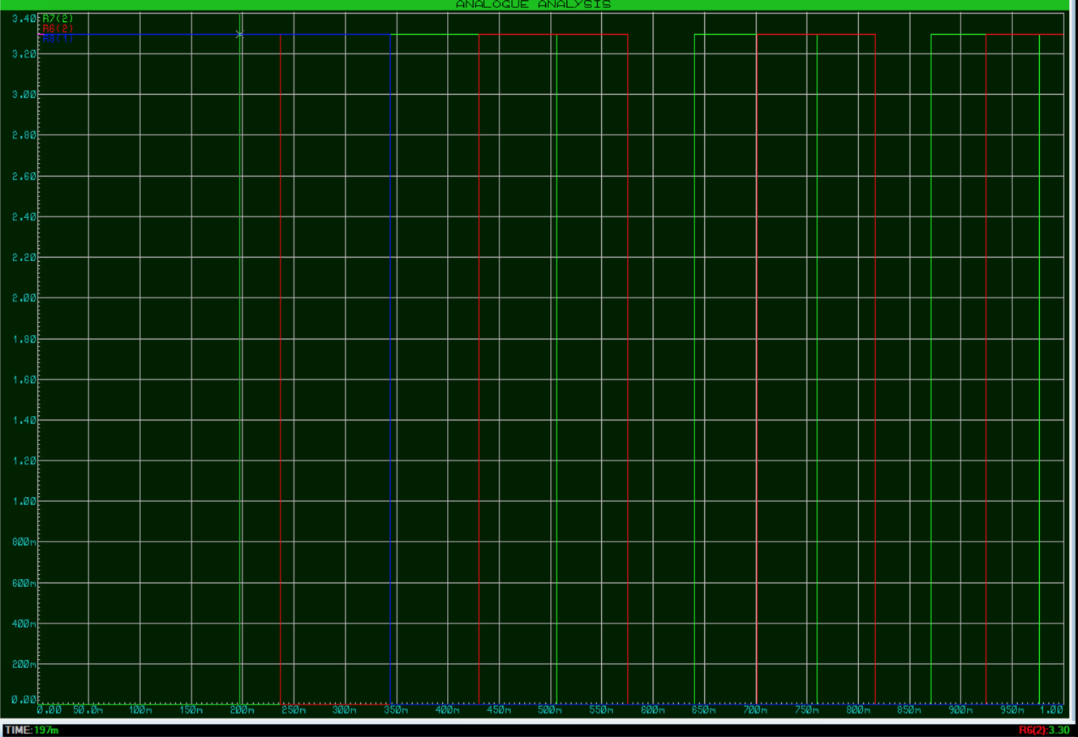
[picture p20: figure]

Fig. 20: Analog Analysis of the adjusted simulated input to the MCU

## SPST Push Button

### Summary

Item | Description
Purpose | A simple switch mechanism that will be used for user input as key buttons and as limit and collision switches.
Device physical domain and range | The device will detect when a physical object interacts with it.
Device type chosen | Push Button
Proteus Library component name | BUTTON
Device input / output properties | The device will input a constant voltage and output high if an object interacts with it. Although when not enabled, the output is an open circuit, it acts as ground.
Device input / output range | The device has a working voltage of 3.3V. There is no min/max input/output voltage since it is directly communicating a constant voltage.
MCU connectivity details | A digital input pin will be needed to read each push button.
Device/MCU interfacing details | Output: (D/D), no interfacing will be needed.

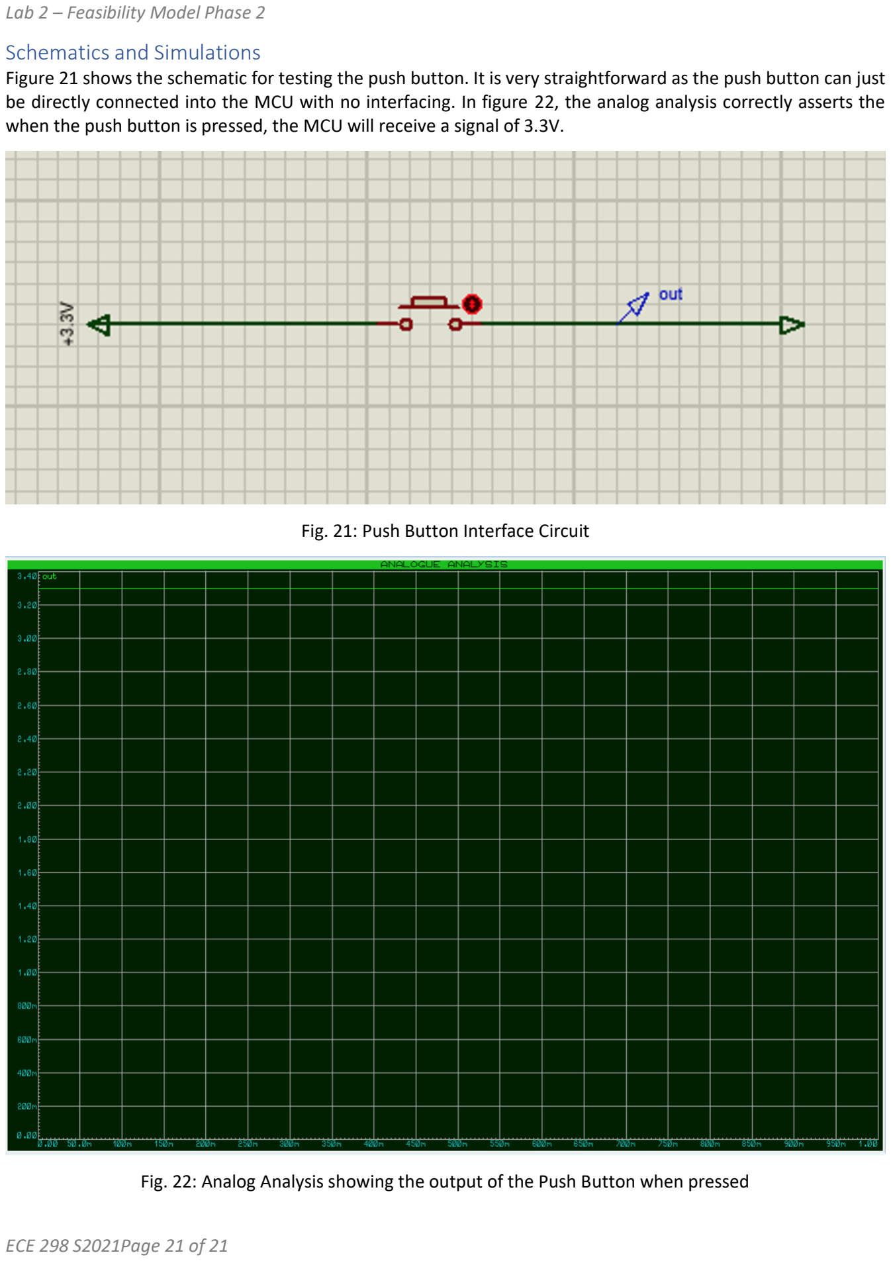
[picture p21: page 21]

### Schematics and Simulations

Figure 21 shows the schematic for testing the push button. It is very straightforward as the push button can just be directly connected into the MCU with no interfacing. In figure 22, the analog analysis correctly asserts the when the push button is pressed, the MCU will receive a signal of 3.3V.

Fig. 21: Push Button Interface Circuit

Fig. 22: Analog Analysis showing the output of the Push Button when pressed

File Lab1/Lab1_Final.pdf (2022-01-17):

# Lab 1 – Feasibility Model Phase 1

ECE 298 – S2021

Team Members Sophia Liu

Kevin Sisjayawan

Team Number 156

## Part 1 – Project Design Requirements

1. Functional Requirements
1. The system must be able to sense movement of objects once they are in a specified range of distance to the door.
2. The system must be able to open the door once the detected object has entered the specified proximity range and close the door once there are no objects in the given range.
3. The system must be able to stop the door from travelling once a collision is detected, and once it is no longer detected, must allow for the door to continue at a limited linear rate
4. The door must open/close with a speed ramp-up and ramp-down rate when starting and stopping movement.
5. The system must allow the user to specify which mode of operation the door opener will operate in (i.e., locked, setup, and run).
6. The system must allow customization of outside/inside sense distances, time to remain open, speed ramp-up and ramp-down constants when operating under 'setup' mode.
7. The system must have a Liquid Crystal Display (LCD) to show the current mode of operation.
8. The system must have two green Light Emitting Diodes (LED) to show when an object has been detected within the range of the inside and outside proximity sensors.
9. The system must have a flashing red LED when the door is in motion.
10. The system must have a flashing yellow LED when a collision with the door is detected.
2. Non-functional Requirements
1. The door closing/opening operations should be time efficient.
2. Energy losses due to heating and cooling (primarily from hot/cool air coming through the door) should be minimized.
3. The door system must operate in a safe manner that will not cause harm to the user.
4. The door motor drive must be power efficient.
3. Constraint Requirements
1. Only parts from the Proteus libraries can be used.
2. The Printed Circuit Board (PCB) shape must be as per the PCB layout template specified in ECE 298 Lab 4.
3. The final schematic and PCB design must include suitable decoupling capacitors for power supply voltage filtering.
4. Voltage level translations (3.3V to 5V, and 5V to 3.3V) must be used for signals between the STM32 Microcontroller Unit (MCU) and 5V devices where needed.

## Part 2 – Project Considerations for I/O

Lab 1 – Feasibility Model Phase 1

ECE 298 S2021

Project Sensors and User Inputs
- HCSR04 (Ultrasonic Ranger Module)
- Description and use: For the outside and inside proximity sensors.
- Parameters:
■ Max Range: 4m
■ Min Range: 2cm
■ Measuring Angle: 15 degrees
■ Trigger Input Signal: 10uS TTL pulse
■ Working Voltage: 5V
■ Echo Back Pulse Width: every uS / 148 = every inch
- Connection to MCU: MCU's general purpose input/output ports (GPIO) to output trigger pulse and accept returning echo signal.
- ECE298_DCMOTOR_ENCODER
- Description and use: To sense and monitor the direction and number of revolutions of the door motor. Note that this is the same device used as the motor to open and close the door.
- Parameters:
■ Operating Voltage: 4.5V to 5.5V
■ Output: Two digital outputs (quadrature waveform)
- Connection to MCU: MCU's general purpose input/output ports (GPIO) to accept the two output signals, with a pull-up resistor.
- SPST Push Button
- Description and use: For the door position limit switches, collision switch, and the user inputs as a back, enter, up, and down button.
- Parameters:
■ Current Rating: 3A @ 125V AC
■ Initial Contact Resistance: 20 MΩ (max)
- Connection to MCU: MCU's general purpose input/output ports (GPIO) to accept the output signals, with a voltage source.

Project Actuators and User Outputs
- ECE298_DCMOTOR_ENCODER
- Description and use: Motor to open and close the door as specified by the system
- Parameters:
■ Zero load rotations per minute (RPM): 360 RPM
■ Load/max torque ratio: 50%
■ Pulses per revolution: 24 pulses
■ Nominal voltage: 12 V
■ Initial Contact Resistance: 20 MΩ (max)
- Connection to MCU: MCU’s serial interface using the serial peripheral interface to output to a motor controller integrated circuit that will control the motor
- LM016L
- Description and use: LCD to display the current mode the door opener is operating under
- Parameters:
■ Number of columns: 16
■ Number of rows: 2

ECE 298 S2021

■ Clock frequency: 250 kHz
- Connection to MCU: Use the MCU's serial interface to output digital signals to the LCD with the appropriate bit sequence to match the alphanumeric description of the modes
- LED-RED, LED-YELLOW, LED-GREEN
- Description and use: LEDs to signify when an object is within the inside and outside proximity range (LED-GREEN), when the door is in motion (LED-RED), and when the door has collided with an object (LED-YELLOW)
- Parameters¹
:
■ Forward Voltage @ 20mA: 2.2V ■ Full Drive Current: 10 mA
■ Breakdown Voltage: 4V
■ Series Resistance: 3 Ohms
■ Minimum on-time to Light: 10 ms
- Connection to MCU: Use the MCU's GPIO to output a digital signal to an N-channel MOSFET transistor that will 'switch' the LED on or off with a pull up resistor (circuit shown in Part 3)
1 The essential parameters of the different LEDs are taken from the parts properties, which show that all have the same parameters despite emitting different colors (this may be different in the prototyping phase)

Project MCU Internal Resources
Sensors and User Inputs:

For the proximity distance sensor, a timer/clock within the MCU is needed to calculate the length of the signal received. This directly correlates to how far an object is away from the sensor and so the time is used to verify the distance and determine the corresponding functionality. Also software will be needed to convert from the time the signal is active to a usable distance or have an error handler for distances outside a suitable range. The timer and the ratio of motor revolutions to wheel rotations will both be needed to calculate the RPM of the motor. Software to compare the pulses of the two channels will output the direction of the motor. For the position limit switch and collision switches, they can be linked to an interrupt so that the priority will be to halt door movement for safety. After the collision switch is open, the door speed is limited to 0.5ft/sec. To process user inputs, software is needed to handle the different operating modes and the selections that the user will make using the push buttons. All the parameters specified in the set-up mode (inside and outside sense distance, time to remain open at full position, speed ramp-up and ramp-down constant) will be needed by the MCU to properly run the system.

Actuators and User Outputs:

The ECE298_DCMOTOR_ENCODER will require either the serial peripheral interface or inter-integrated circuit interface in order to properly output signals to the motor controller integrated circuit (connected to the motor itself) from the MCU. Parameters needed for the software to properly output to the motor include the desired speed of the motor (to control how fast the motor opens or closes the door), as well as the motor direction (to control whether the door is opening or closing). Controlling motor speed will most likely require a pulse width modulated input. The LM016L LCD display will also require the SPI to set the bit pattern needed by the LCD inputs. In terms of LCD functionality, the MCU software will require as parameters: the LCD initialization/configuration bits, the current operating mode of the door, and the bit encodings (potentially implemented as a look up table) to translate alphanumeric characters to bits. Lastly, the LEDs (i.e. LED-RED, LED-YELLOW, LED-GREEN) will require a clock to make them flash when turned on. MCU GPIO pins should be set to digital output to act as switches to allow for the LED to be turned on or off. The software should have as

ECE 298 S2021

parameters: the current door operation mode to determine which LED (i.e. which color) should be flashed, and some sort of data structure to map what mode corresponds to which color.

## Part 3 – Device Testing Methodology

Ultrasonic Ranger Module - HCSR04

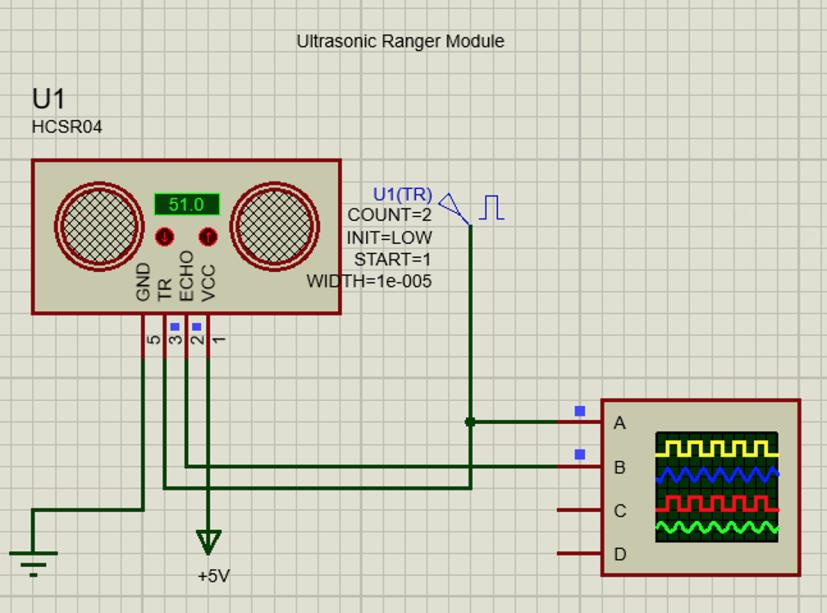
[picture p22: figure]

Fig. 1: Ultrasonic Ranger Circuit Schematic

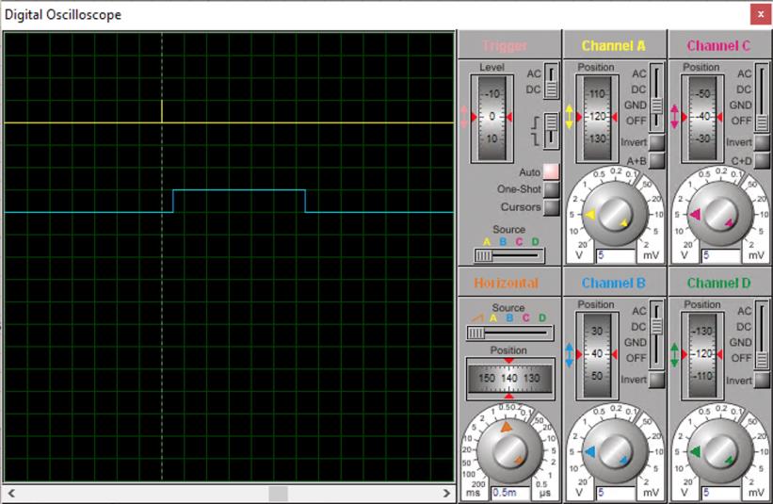
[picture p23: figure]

Fig. 2: Scope Output of Ultrasonic Ranger Circuit

To test the ultrasonic ranger module, the device is preset to detect an object at 51 cm (20 inches) and a trigger pulse of width 10 us is inputted to start the ranging. An output echo signal is detected, ensuring that the module is working correctly. To further verify the device’s expected output, we can calculate that the width of the output signal should follow the equation: uS / 148 = inch. Since our input is 20 inches, the output width should be 2960

ECE 298 S2021

us. Looking at the digital analysis graph, the signal is high for (3230 - 272) us = 2958 us, which agrees with our theoretical calculations. Testing with parameters of 2, 4, 6, 8 feet all produce an expected outcome. This is satisfactory for our project requirements to be used as the inside and outside distance proximity sensors since it can successfully detect objects within the required sense distances and the output is readable and simple enough for the MCU to process. So, when an object is detected within the device’s range but not within our system’s sense distances, the MCU can decide to ignore the signal until a shorter, more suitable signal is detected.

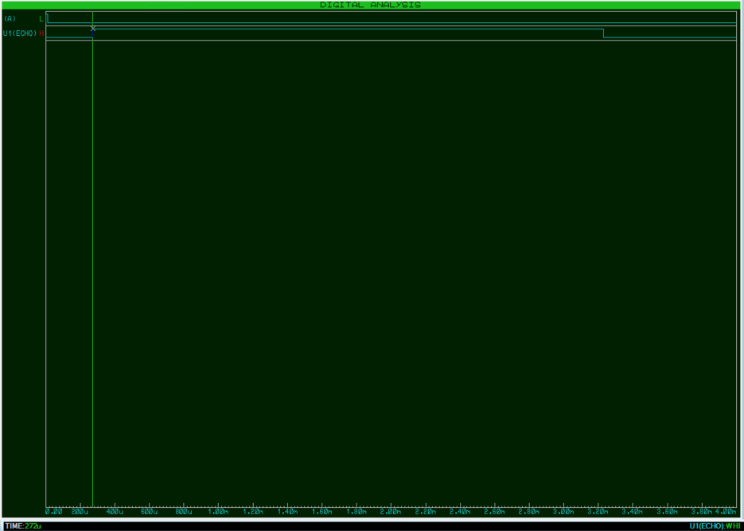
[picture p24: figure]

Fig. 3: Digital Analysis Graph of Ultrasonic Ranger Circuit (1)


Fig. 4: Digital Analysis Graph of Ultrasonic Ranger Circuit (2)

ECE 298 S2021

Push Button - SPST Push Button


Fig. 5: Push Button Circuit Schematic (on)


Fig. 6: Push Button Circuit Schematic (off)

Pushing the push button is tested by observing the voltage change when the button is in the down and up position. An LED is also added to show that when the button is not pushed, it is unlit, but when the button is pushed down, it is on. Based on the LED and the digital analysis graph, you can see that the voltage only passes through when the button is pushed down, to form a complete circuit. This push button’s behaviour will be useful throughout many aspects of our project. Firstly, for the door limit switches, when the door hits its max and min

ECE 298 S2021

travel limits, the door will push onto the button, telling the MCU the door needs to stop travelling. Similarly, for the collision switch, any time the button on the door is pushed, an interrupt signal will stop all door movement for the duration of the button press. The push button will also be used to detect user inputs. Four buttons are used to indicate back, enter, up and down so the user can easily navigate through the different types of operating modes and select the parameters they would like to customize for the system.

DC Motor and Encoder - ECE298_DCMOTOR_ENCODER
There are several aspects of the DC Motor and Encoder which need to be tested, and as a result there are multiple test schematics for each respective attribute to be investigated.

The first test is to show that the DC motor is able to be reversed in direction and that the attached encoder will appropriately show this reverse in polarity. Two circuits are made to model this behavior. The first circuit is a simple 1V DC power supply output into the motor, which is grounded. Voltage probes are placed at the Q1, IDX, and Q2 outputs from the encoder and are output into a digital analysis graph. The second circuit is the same as the first, with the DC power supply changed to -1V to reverse polarity. The digital analysis graph shows that the IDX output creates a pulse every 24 revolutions. This verifies the property as set in part 1 of this report that the motor will have 24 pulses per revolution. Furthermore, it means that it would be possible to calculate the number of revolutions the motor has spun for – a parameter that will be required. As a sanity check, one can also verify that M1(Q2) and M2(Q2) have the same output, as they should. The graph shows that when M1(Q1) has a rising edge, M2(Q1) has a falling edge and vice versa. This indicates the reverse in polarity, showing that whichever direction the motor measured by M1(Q1) is spinning, the motor measured by M2(Q1) is spinning the opposite direction. One can also verify this in the circuit schematic that shows that motor 1 is spinning at +15 RPM, whereas motor 2 is spinning at -15 RPM. This not only shows that the motor is reversible, but also that it is possible to detect which direction the motor is turning by comparing Q1 and Q2 rising/falling edges – another parameter that will be needed. Thus, this motor will be viable for the purposes of this project.


Fig. 7: Motor Direction Testing Schematic


ECE 298 S2021

Fig. 8: Motor Direction Testing Output

The next test is to have a rough estimate of the full-power startup inrush current of the motor. The circuit required for this test is a 12V DC input into the motor with an ammeter in series, alongside one voltage probe METER1(-) and one current probe M3(-) that outputs to an analogue analysis graph. Upon running the simulation, one can see that the current jumps immediately to a value of around 1A. As such, when choosing an appropriate motor controller integrated circuit in the future, it is important to consider that it must be able to handle a maximum current of 1A. This is a relatively high current for integrated circuits, and as such will most probably limit the range of selection of motor controllers available for this project. At its maximum RPM, the motor is shown in the analogue analysis to approach a current minimum of around 500mA. As such, this would also be a good estimate of the operational low bound of the motor controller IC. However, given a range from 500mA– 1A, this motor will be viable for this project.

Fig. 9: Motor Inrush Current Test Schematic


ECE 298 S2021

Fig. 10: Motor Inrush Current Test Output

The next test is to see the performance of the motor under battery degradation conditions (i.e. at different input voltages). The motor is connected similarly to the previous test, the only difference being that the input is now modelled as varying voltages at different times. For testing purposes, the voltages are chosen to be 0V, 6V, 10V, 12V, 10V, 6V, 0V in that order. METER2(-) and M4(-) show the motor voltage and current, respectively. A calculation of the total power consumption is beyond the scope of this test, but one thing to note is that at its peak RPM of 180 RPM, the motor has a voltage of 12V, a current of around 525mA, and thus consumes around 6.3W of power. This is a relatively high value, and will be important for considerations when selecting the motor power supply, as it should be able to compensate for that upper limit.

Fig. 11: Current Voltage Curve Motor Schematic


ECE 298 S2021

Fig. 12: Current Voltage Curve Motor Output

The last test is to simulate motor performance using a pulse width modulated input, as this best reflects what the actual implementation of the motor controller circuit will look like. The circuit schematic is similar to all tests before, with the only difference being that the input signal is now a user-defined PWM signal in a text file. METER3(-) and M5(-) measure the motor voltage and current respectively and are correspondingly plotted on the analogue analysis graph. The graph shows the current characteristics of the motor as varying widths of the PWM voltages (all of which are set at 12V) are input into the motor. Though it was rather difficult to measure the exact RPM and speed of the motor at the varying PWM inputs, in general, the graph shows sharp increases in current as the motor speed increases. It can also be seen that the decay of the current has a relatively long time constant, resulting in large current modulation as a result of the modulating input. The largest variance seems to come from the second ‘step’ of the current in the graph, ranging from 250mA to 600mA (i.e. a range of 350mA). This is a rather high range and will be a useful property for consideration in properly dealing with the current across the motor. In the case of this test, the motor is merely grounded and as such has no effect on anything. However, if the motor is connected to an IC or other device (as may be the case in the future), this modulating current may damage other components. But all in all, this test serves to show the performance of the motor in a more realistic setting for future considerations.


ECE 298 S2021

Fig. 13: PWM Motor Schematic

Fig. 14: PWM Motor Output

Liquid Crystal Display - LM016L

Fig. 15: LCD Test Bit Pattern


ECE 298 S2021

Fig. 16: LCD Test Schematic

To test the LCD, a pattern generator is used to output the bit pattern of the binary ASCII values corresponding to “1”, “5”, and “6” to spell out the group number 156. First, the pattern generator had to initialize the LM016L as described in the device datasheet (the bits can be seen in address 0x13 and below). Afterwards, the bit pattern (i.e. from address 0x15 to 0x26) is sent through the D4–D7 pins of the LCD. This sent 4 bits of the bit pattern at a time. The pattern generator uses an internal clock that runs at 4.403 Hz, and a reset rate at 500 mHz. For testing purposes, this is adequate to verify that the given bit pattern would produce the desired output. However, when prototyping it is important to note that the clock rate will be determined by the MCU and thus may be changed. To verify that the given bit pattern would output the correct result, the simulation once run will output “156” onto the LCD. No scope figures are required since this test produces a visual output that can be easily read. Given that outputting onto the LCD works, this device will be adequate enough for the purposes of our project. Furthermore, a 16x2 display would be large enough to output any required alphanumeric string symbolizing a given mode of operation.


ECE 298 S2021

Light Emitting Diodes - LED-RED, LED-GREEN, LED-YELLOW

Fig. 17: LED Test Schematic (on)

Fig. 18: LED Test Results (on)

To test the LEDs, the circuit of how an LED will connect to an MCU GPIO is modelled in the above circuit schematic by replacing the MCU with a digital signal Q1. This signal is connected to the gate channel of an n-channel Metal Oxide Semiconductor Field Effect Transistor (MOSFET) whose source is grounded and whose drain is connected to an LED powered with a 145 Ohm pull-up resistor and 5V DC power supply. Effectively, the n-channel MOSFET acts as a switch, where a high signal input into the gate will allow current to flow through the transistor, and thus also through the LED. This is reflected by the voltage drop measured at D1(K), D2(K),


ECE 298 S2021

and D3(K) as shown both in the circuit schematic as well as the digital analysis graph. The voltage at those points is near to 0V, indicating a voltage drop across the LED and resistor of around 5V in total (which corresponds to the power supply). This shows that with a high digital input signal, the current flows properly through the LED and thus turns on (shown by the colored background of the LED symbols). Note that for testing purposes, all MOSFETS share the same input gate signal Q1. But in reality, each MOSFET will be connected to their individual MCU GPIO pins. Given that the LED functions as expected, it will be viable for the project. Furthermore, the use of a transistor as a ‘switch’ will reduce complications of having to convert MCU GPIO signals to valid input for the LED, given that the LED is powered by the DC supply of 5V.

Below is an example of a low signal being output into the transistors, symbolizing the ‘off’ state of the LEDs. With a low signal, no current is allowed to flow through the transistor to ground, and thus there is no observed voltage drop across the LED. This is reflected by the measurements at D1(K), D2(K), and D3(K) in both the circuit schematic as well as the digital analysis graph which all show 5V. The lack of voltage drop across the resistor and LED indicate that there is no current flowing through the circuit and thus the LED is turned off (as shown by the black colored background of the LED symbol). This verifies that the LED is also capable of being turned off using the same setup as above, and thus will be usable for the purposes of this project.

Fig. 19: LED Test Schematic (off)


ECE 298 S2021

Fig. 20: LED Test Results (off)

## Part 4 – System-Level Design

Fig. 21: High Level Design

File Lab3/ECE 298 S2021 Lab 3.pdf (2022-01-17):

# Lab 3 – Prototype Phase 1

ECE 298 – S2021

Lab Section: | Group: | Team 156
Part 1 – Pin Mapping MCU Pin | Pin Mode | Functional Description
PA8 | GPIO_Output | Toggles the outside green LED output
PA9 | GPIO_Output | Toggles the inside green LED output
PA10 | GPIO_Output | Toggles the red LED output
PA11 | GPIO_Output | Toggles the yellow LED output
PC6 | USART6_TX | Controls the LCD output for ASCII display
PB14 | TIM1_CH2N | Motor driver input 1 with PWM
PB13 | TIM1_CH1N | Motor driver input 2 with PWM
PB5 | GPIO_EXTI5 | START button that sends interrupt request to choose mode of operation
PB6 | GPIO_EXTI6 | ENTER button that sends interrupt request to select device options and parameters
PB7 | GPIO_EXTI7 | SCROLL button that sends interrupt request to scroll through available mode and parameter options
PC0 | GPIO_EXTI0 | Open limit switch to detect when the door is fully opened
PC1 | GPIO_EXTI1 | Close limit switch to detect when the door is fully closed
PC2 | GPIO_EXTI2 | Collision switch to detect when the door has collided against an object
PA12 | GPIO_EXTI12 | Reads the IDX output pulse from the motor encoder for speed control
PB8 | GPIO_EXTI8 | Reads Q1 signal as a trigger to toggle red LED on/off (i.e. flashing)
PC9 | GPIO_Output | Output to send 10 microsecond signals to outside ultrasonic module
PC11 | GPIO_Output | Output to send 10 microsecond signals to inside ultrasonic module
PC10 | GPIO_EXTI10 | Outside ultrasonic response output to be processed by the MCU
PB9 | GPIO_EXTI9 | Inside ultrasonic response output to be processed by the MCU
Part 2 – MCU Resources MCU Resource | Functional Description
USART6 | Communicates with the LCD screen module
TIM1 | Generates PWM signal for DC motor driver inputs
TIM2 | Generates 1MHz timer to be used for measuring length of output signal from ultrasonic modules to calculate distance to an object
GPIO | Only used as outputs to LEDs, and ultrasonic module
NVIC | Enables use of interrupts for push buttons, ultrasonic readings and motor encoder signals (Q1 and IDX)

Lab 3 – Prototype Phase 1


ECE 298 S2021Page 2 of 21

Part 3 – Test Cases Notable changes made to the circuit schematic in Lab 3 compared to the designs of Lab 1 and Lab 2:

- The back button was removed to simplify user inputs
- The up/down button was replaced by a scroll button to simplify user inputs
- Pull-down resistors are added to the push buttons to sink voltage when not pressed
- The LM016L LCD was replaced with the MILFORD-2x16-BKP
- The LCD interface was replaced with the internal UART tools provided by the MCU
Check the "Operational Overview.docx" document for how to run the system. Note that the LCD display requires waiting 500 ms before using it. As such, when running simulations, please always wait at least 500 ms before starting.
Currently, the door motor will continue rotating until one of the limit switches is pushed. Also, all MCU interfaces are the same as those from Lab2 (excluding the LCD display). As such, as calculated in Lab2, the current drawn from those pins are within the limits of the MCU.
Note that the Open Limit Switch, Close Limit Switch, and Collision Switches are interrupts that run in whatever state the current system is in. For the purposes of brevity, they are only tested in the LOCK mode in Tests 4, 5, 6. But it is possible to run those same tests in any other mode and they will still be fully functional. These tests were also run in the SETUP and RUN modes but not included in this report to avoid repetition.
Overall Schematic:

Fig. 0.1: Overall Schematic


Fig. 0.2: LED Schematics

Fig. 0.3: Motor and encoder schematic


Fig. 0.4: LCD Schematic


Fig. 0.5: Inside ultrasonic schematic


Fig. 0.6: Outside Ultrasonic Schematic

Fig. 0.7: Push Button schematics

Test 1: Changing Operating Modes
Requirement | User must be able to change the operating mode of the system at any point and select out of three options: RUN, SETUP, LOCK
Test Setup | 1. Press START 2. Go through the instructions, scroll and select LOCK 3. Press START 4. Go through instructions, scroll and select SETUP 5. Press START 6. Go through instructions, scroll and select RUN
Expected Outcome | 1. START button displays instructions on LCD 2. Selecting LOCK enters LOCK mode and displays it on LCD 3. Selecting SETUP enters SETUP mode and displays it on LCD 4. Selecting RUN enters RUN mode and displays it on LCD
Operational | Yes
What's Not Working | N/A

Schematics and Simulations


Fig. 1.1: Initial Main Menu

Fig. 1.2: First Option for Operational Mode (Setup)


Fig. 1.3: Second Option for Operation Mode (Run)


Fig. 1.4: Third Option for Operation Mode (Lock)


Fig. 1.5: Next Screen After Selecting an Operation Mode


Fig. 1.6: Selecting the Setup Mode


Fig. 1.7a: Error Message in Run Mode Since Parameters Haven't Been Setup


Fig. 1.7b: Selecting the Run Mode After Parameters Have Already Been Setup


Fig. 18: Selecting the Lock Mode Test 2: Locked Mode (Open)
Requirement | When selecting LOCK mode, the user must be able to choose the OPEN option to lock the system in an opened door position.
Test Setup | 1. Press START 2. Go through the instructions, scroll, and select LOCK 3. Press START 4. Go through the instructions, scroll, and select OPEN option
Expected Outcome | 1. The LCD displays instructions on selecting the LOCK mode operation 2. When entering the OPEN LOCK mode the motor begins to rotate with a negative RPM and the RED LED begins to flash
Operational | Yes
What's Not Working | N/A

Schematics and Simulations

Fig. 2.1: First Entering the Lock Mode


Fig. 2.2: Open Door Option in the Lock Mode

Fig 2.3: Operating in the Lock Mode with Motor Rotating (-ve RPM) and RED LED Flashing

Test 3: Locked Mode (Close)
Requirement | When selecting LOCK mode, the user must be able to choose the CLOSE option to lock the system in a closed door position.
Test Setup | 1. Press START

| 2. Go through the instructions, scroll, and select LOCK 3. Press START 4. Go through the instructions, scroll, and select CLOSE option
Expected Outcome | 1. The LCD displays instructions on selecting the LOCK mode operation 2. When entering the CLOSE LOCK mode the motor begins to rotate with a positive RPM and the RED LED begins to flash
Operational | Yes
What's Not Working | N/A

Schematics and Simulations

Fig. 3.1: First Entering the Lock Mode

Fig. 3.2: Close Door Option in the Lock Mode


Fig 3.3: Operating in the Lock Mode with Motor Rotating (-ve RPM) and RED LED Flashing

Test 4: Open Limit Switch
Requirement | When the open limit switch has been hit, the system must signal to the motor that the door is fully opened, and thus the motor must ramp down and stop running.
Test Setup | 1. Press START 2. Go through the instructions, scroll, and select LOCK 3. Press START 4. Go through the instructions, scroll, and select OPEN option 5. Wait 5 seconds 6. Press OPEN LIMIT SWITCH button
Expected Outcome | 1. When the OPEN LIMIT SWITCH button has been pressed, the motor begins to ramp down and eventually stops rotating
Operational | Yes
What's Not Working | N/A

Schematics and Simulations


Fig. 4.1: Graph of Motor on Hitting Open Limit and Ramping Down to Stop
Test 5: Close Limit Switch
Requirement | When the close limit switch has been hit, the system must signal to the motor that the door is fully closed, and thus the motor must ramp down and stop running.
Test Setup | 1. Press START 2. Go through the instructions, scroll, and select LOCK 3. Press START 4. Go through the instructions, scroll, and select CLOSE option 5. Wait 5 seconds 6. Press CLOSE LIMIT SWITCH button
Expected Outcome | 1. When the CLOSE LIMIT SWITCH button has been pressed, the motor begins to ramp down and eventually stops rotating
Operational | Yes
What's Not Working | N/A

Schematics and Simulations


Fig. 5.1: Graph of Motor on Hitting Close Limit and Ramping Down to Stop
Test 6: Collision Switch
Requirement | When the collision switch has been hit, the YELLOW LED should start flashing and the motor should ramp down and stop so long as the push button has been pressed. When the button is released, the motor should start rotating with a positive RPM at 0.5 ft/sec until the door is closed.
Test Setup | 1. Press START 2. Go through the instructions, scroll, and select LOCK 3. Press START 4. Go through the instructions, scroll, and select OPEN option 5. Wait 5 seconds 6. Press and hold the COLLISION SWITCH button 7. Wait 5 seconds 8. Release the COLLISION SWITCH button
Expected Outcome | 1. When the COLLISION SWITCH button has been pressed and held down, the YELLOW LED should flash while the button is held down and the motor should ramp down to an eventual stop 2. When the COLLISION SWITCH button has been released, the YELLOW LED should stop flashing and the motor should begin rotating at a maximum of 45 RPM (converts to a maximum of 0.5 ft/sec)

Operational | Yes
What's Not Working | N/A

Schematics and Simulations


Fig. 6.1: Collision Switch Pressed Down Causing YELLOW LED to flash and Motor to Ramp Down

Fig. 6.2: Collision Switch Graph on Collision & Restart
Test 7: Setup Mode (Selecting Parameters P1, P2, P3, P4, P5)
Requirement | User must be able to select values for each parameter (P1, P2, P3, P4, P5) so the system can operate using the selected values.
Test Setup | 1. Press START 2. Go through the instructions, scroll, and select SETUP 3. Go through the instructions, scroll, and select any value for P1 4. Repeat step 3 for P2, P3, P4, and P5
Expected Outcome | 1. The LCD displays the appropriate instructions for each step of the setup mode 2. The system records the value of the parameter
Operational | Yes
What's Not Working | N/A

Schematics and Simulations


Fig. 7.1: In the Setup Mode


Fig. 7.2: Option 1 (2ft) for Parameter P1


Fig. 7.3: Option 3 (6ft) for Parameter P2

Fig. 7.4: Screen Display After Selecting Parameter P1

Test 8: Run Mode (Normal Operation)
Requirement | User must be able to run the system properly as described in the Lab project description after having properly gone through the SETUP mode.
Test Setup | 1. Set the outside ultrasonic module to have an object at 1000 cm 2. Set the inside ultrasonic module to have an object at 2 cm 3. Press START 4. Go through the instructions, scroll, and select SETUP 5. Go through the instructions, scroll, and select the following values: ● P1 = 2 ft ● P2 = 8 ft ● P3 = 20 seconds ● P4, P5 = any value 6. Press START 7. Go through the instructions, scroll, and select RUN 8. Enter the RUN mode 9. Wait 2 seconds then press OPEN LIMIT SWITCH
Expected Outcome | 1. LCD Displays that the system is running when entering RUN mode 2. The inside GREEN LED should be on and the outside GREEN LED should be off when running 3. The motor should open (negative RPM) when entering the RUN mode (since there is an object within the boundary) 4. The motor should stop once the door is fully opened (OPEN LIMIT SWITCH pressed) 5. The system should wait 20 seconds before closing the door again
Operational | Expected outcomes 1-4 are working
What's Not Working | The system doesn't wait 20 seconds and then close the door again because the ultrasonic module is set in the beginning and when the proteus simulation is running, it's not possible to change the module's properties. As a result, the software always detects that there is an object detected by the inside ultrasonic module. Because of this, the inside GREEN LED never turns off, and the door will never close. To correct this, there needs to be another way to simulate an object being detected by the ultrasonic module. A possible solution is to instead have a digital pulse input to simulate the ultrasonic module, where the pulse is so that the ultrasonic detects an object within the distance once every 10 seconds or so. Thus, the software is correct, but the hardware is not.

Schematics and Simulations


Fig. 8.1: Run Mode with Object in Boundary Detected by Inside Ultrasonic Module
Test 9: Run Mode (Different Ramp-up/Ramp-down Speed Constant)
Requirement | User must be able to change the ramp-up speed to change the speed of the motor.
Test Setup | 1. Set the outside ultrasonic module to have an object at 500 cm 2. Set the inside ultrasonic module to have an object at 2 cm 3. Press START 4. Go through the instructions, scroll, and select SETUP 5. Go through the instructions, scroll, and select the following values: ● P1 = 2 ft ● P2 = 8 ft ● P3 = any value ● P4 = Level 4 ● P5 = Level 1 6. Press START 7. Go through the instructions, scroll, and select RUN 8. Enter the RUN mode 9. Wait 2 seconds then press OPEN LIMIT SWITCH
Expected Outcome | 1. LCD Displays that the system is running when entering RUN mode 2. The inside GREEN LED should be on and the outside GREEN LED should be off when running 3. The motor should open with a faster ramp-up speed (more negative RPM) when entering the RUN mode (since there is an object within the boundary) 4. Once the OPEN LIMIT SWITCH button has been pressed, the motor should ramp down with a lower speed

Operational | Expected outcomes 1-3 are working.
What's Not Working | The software as implemented does not have a way to properly setup the ramp-down to correlate to the set parameter P5. This is because the current way the motor_off helper function is implemented merely sets both channels to the motor driver inputs to 0 volts. As such, the ramp-down constant, though settable in SETUP mode is technically unchangeable. This makes the software incorrect, but the hardware correct.

Schematics and Simulations


Fig. 9.1: Run Mode with Object in Boundary Detected by Inside Ultrasonic Module


Fig. 9.3: Motor Ramping Up and Ramping Down

Fig. 9.2: Ramp-down Incorrect Software Section



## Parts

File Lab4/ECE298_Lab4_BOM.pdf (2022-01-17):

## Bill Of Materials for ECE298_Lab4

Design Title | ECE298_Lab4

### Author Document Number Revision

Design Created | December 15, 2020

### Design Last Modified August 6, 2021 Total Parts In Design 57

0 Modules
Quantity | References | Value | Stock Code
Sub-totals:
8 Capacitors
Quantity | References | Value | Stock Code
4 | C1-C2,C4,C6 | 10u | Digikey 478-1417-2-ND
4 | C3,C5,C16-C17 | 0.1u | Digikey 311-1047-1-ND
Sub-totals:
17 Resistors
Quantity | References | Value | Stock Code
9 | R1-R2,R4,R8-R13 | 10k | 72-0869
4 | R3,R5-R7 | 200R | 72-0615
2 | R14-R15 | 47k | 72-0949
2 | R16-R17 | 91k | 72-0973
Sub-totals:
1 Integrated Circuits
Quantity | References | Value | Stock Code
1 | U10 | DRV8871
Sub-totals:
6 Transistors
Quantity | References | Value | Stock Code
2 | Q1,Q10 | BSS138
4 | Q2-Q5 | 2N7002
Sub-totals:
0 Diodes
Quantity | References | Value | Stock Code
Sub-totals:
25 Miscellaneous
Quantity | References | Value | Stock Code
2 | CN7,CN10 | 1-534236-9 | 1-534236-9
10 | J1-J2,J4-J6,J17-J21 | CONN-SIL2
1 | J7 | 26630301RP2 | NorComp 26630301RP2
2 | J8,J11 | CONN-SIL4
1 | J10 | CONN-SIL7
1 | J12 | TBLOCK-I2
8 | J13-J16,J31,J33,J38-J39 | PIN
Sub-totals:

Totals:

| | | August 6, 2021 12:26:21 AM

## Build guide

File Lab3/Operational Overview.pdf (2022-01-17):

Operational Overview:
The system begins in an empty state. To start, press the START button and the LCD will display instructions to select an operational mode. The three operational modes are SETUP, RUN, and LOCK. Press the SCROLL button to scroll through the options and press the ENTER button to select the mode displayed.
If in the SETUP mode, instructions will appear on the LCD to select the parameters. The LCD will iterate through P1, P2, P3, P4, P5, and show the available values for each parameter. Once a value has been chosen for a parameter, the LCD will iterate through to the next parameter and show the values for that parameter. Once the parameters have been properly set, the system will ask the user to press the START button. At this point, the user can decide to enter RUN mode or any of the other modes. To exit at any stage, press the START button. Note that an incomplete setup will prevent the user from entering the RUN mode.
If in the RUN mode, instructions will appear on the LCD to run the system. If the system has not been initialized properly using the SETUP mode, then the system will not begin running. Otherwise, it will run with the given parameters.
If in the LOCK mode, instructions will appear on the LCD to decide which locked mode (open or closed) to run. Press SCROLL to go through the options and press ENTER to select one. Once selected, the system will either fully open or close the door in the LOCK state.

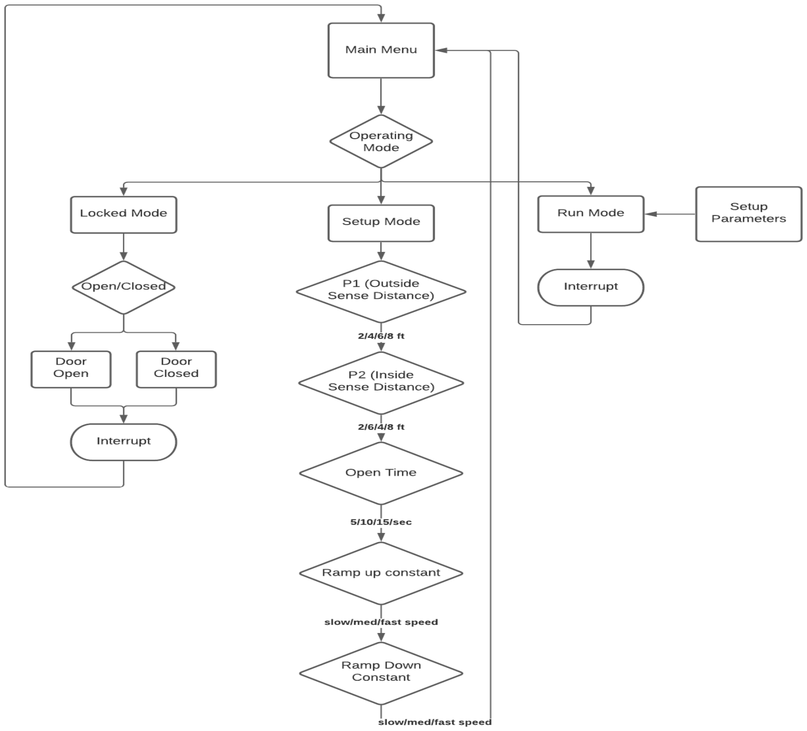
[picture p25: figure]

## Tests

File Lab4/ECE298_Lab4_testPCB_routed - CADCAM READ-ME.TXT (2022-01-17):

LABCENTER PROTEUS TOOL INFORMATION FILE
=======================================

In case of difficulty, please e-mail support@labcenter.co.uk

Tool set up for Proteus layout 'ECE298_Lab4.pdsprj'.
CADCAM generated at 12:24:26 AM on August 6, 2021.

File List
---------
Top Copper              : ECE298_Lab4_testPCB_routed - CADCAM Top Copper.GBR
Bottom Copper           : ECE298_Lab4_testPCB_routed - CADCAM Bottom Copper.GBR
Top Silk Screen         : ECE298_Lab4_testPCB_routed - CADCAM Top Silk Screen.GBR
Bottom Silk Screen      : ECE298_Lab4_testPCB_routed - CADCAM Bottom Silk Screen.GBR
Top Solder Resist       : ECE298_Lab4_testPCB_routed - CADCAM Top Solder Resist.GBR
Bottom Solder Resist    : ECE298_Lab4_testPCB_routed - CADCAM Bottom Solder Resist.GBR
Top SMT Paste           : ECE298_Lab4_testPCB_routed - CADCAM Top SMT Paste.GBR
Bottom SMT Paste        : ECE298_Lab4_testPCB_routed - CADCAM Bottom SMT Paste.GBR
Mechanical 1            : ECE298_Lab4_testPCB_routed - CADCAM Mechanical 1.GBR
Top Assembly            : ECE298_Lab4_testPCB_routed - CADCAM Top Assembly.GBR
Bottom Assembly         : ECE298_Lab4_testPCB_routed - CADCAM Bottom Assembly.GBR
Drill, Plated, 1-16     : ECE298_Lab4_testPCB_routed - CADCAM Drill TOP-BOT Plated.GBR
Netlist                 : ECE298_Lab4_testPCB_routed - CADCAM Netlist.IPC

Photoplotter Setup
------------------
Format: X2, ASCII, 4.3, metric, absolute, eob=*, LZO
Bounds: -35mm -32mm 35mm 30mm
Notes:  D=Diameter, S=Side, W=Width, H=Height, C=Chamfer, I=Index

D10	CIRCLE  D=0.381mm                                                         DRAW  Conductor
D11	CIRCLE  D=0.203mm                                                         DRAW  Conductor
D12	CIRCLE  D=1.016mm                                                         FLASH ViaPad
D13	CIRCLE  D=0.508mm                                                         FLASH ViaPad
D14	SQUARE  S=1.27mm                                                          FLASH ComponentPad
D15	CIRCLE  D=1.524mm                                                         FLASH ComponentPad
D16	CIRCLE  D=2.032mm                                                         FLASH ComponentPad
D17	CIRCLE  D=3.048mm                                                         FLASH ComponentPad
D18	RECT    W=0.61mm              H=1.549mm                                   FLASH SMDPad,CuDef
D19	RECT    W=3.15mm              H=2.438mm                                   FLASH SMDPad,CuDef
D70	RECT    W=1.016mm             H=1.27mm                                    FLASH SMDPad,CuDef
D71	SQUARE  S=2.032mm                                                         FLASH ComponentPad
D20	RECT    W=1.016mm             H=0.889mm                                   FLASH SMDPad,CuDef
D21	RECT    W=1.27mm              H=1.016mm                                   FLASH SMDPad,CuDef
D22	RECT    W=0.889mm             H=1.016mm                                   FLASH SMDPad,CuDef
D23	CIRCLE  D=1.397mm                                                         FLASH WasherPad
D24	CIRCLE  D=0.203mm                                                         DRAW  Profile
D25	RECT    W=1.143mm             H=1.448mm                                   FLASH SMDPad,CuDef
D26	SQUARE  S=0.61mm                                                          FLASH SMDPad,CuDef
D27	CIRCLE  D=0.203mm                                                         DRAW  Material
D28	CIRCLE  D=0.25mm                                                          DRAW  Material
D29	CIRCLE  D=0.2mm                                                           DRAW  Material
D72	CIRCLE  D=0.1mm                                                           DRAW  Material
D73	CIRCLE  D=0.508mm                                                         DRAW  Material
D30	CIRCLE  D=0.152mm                                                         DRAW  Material
D31	CIRCLE  D=1.27mm                                                          FLASH Material
D32	CIRCLE  D=0.813mm                                                         FLASH Material
D33	PPAD    W=1.524mm             H=1.524mm             I=0                   FLASH Material
D34	CIRCLE  D=1.778mm                                                         FLASH Material
D35	CIRCLE  D=2.286mm                                                         FLASH Material
D36	CIRCLE  D=3.302mm                                                         FLASH Material
D37	PPAD    W=0.61mm              H=1.549mm             I=1                   FLASH Material
D38	PPAD    W=3.15mm              H=2.438mm             I=2                   FLASH Material
D39	PPAD    W=1.27mm              H=1.524mm             I=3                   FLASH Material
D40	PPAD    W=2.286mm             H=2.286mm             I=4                   FLASH Material
D41	PPAD    W=2.286mm             H=2.286mm             I=5                   FLASH Material
D42	PPAD    W=1.27mm              H=1.143mm             I=6                   FLASH Material
D43	PPAD    W=1.524mm             H=1.27mm              I=7                   FLASH Material
D44	PPAD    W=1.143mm             H=1.27mm              I=8                   FLASH Material
D45	CIRCLE  D=1.651mm                                                         FLASH Material
D46	PPAD    W=1.143mm             H=1.448mm             I=9                   FLASH Material
D47	PPAD    W=0.61mm              H=0.61mm              I=10                  FLASH Material
D48	RECT    W=0.61mm              H=1.549mm                                   FLASH Material
D49	RECT    W=3.15mm              H=2.438mm                                   FLASH Material
D50	RECT    W=1.016mm             H=1.27mm                                    FLASH Material
D51	RECT    W=1.016mm             H=0.889mm                                   FLASH Material
D52	RECT    W=1.27mm              H=1.016mm                                   FLASH Material
D53	RECT    W=0.889mm             H=1.016mm                                   FLASH Material
D54	RECT    W=1.143mm             H=1.448mm                                   FLASH Material
D55	SQUARE  S=0.61mm                                                          FLASH Material
D56	CIRCLE  D=0.203mm                                                         DRAW  Slot
D57	CIRCLE  D=0.085mm                                                         DRAW  Material
D58	CIRCLE  D=1.219mm                                                         DRAW  Material
D59	CIRCLE  D=0.314mm                                                         DRAW  Material
D60	CIRCLE  D=0.05mm                                                          DRAW  Material
D61	CIRCLE  D=0.549mm                                                         DRAW  Material
D62	CIRCLE  D=0.196mm                                                         DRAW  Material
D63	CIRCLE  D=0.073mm                                                         DRAW  Material
D64	CIRCLE  D=0.813mm                                                         DRAW  Material
D65	CIRCLE  D=0.178mm                                                         DRAW  Material
D66	CIRCLE  D=0.406mm                                                         DRAW  Material
D67	CIRCLE  D=0.097mm                                                         DRAW  Material
D68	CIRCLE  D=0.11mm                                                          DRAW  Material
D69	CIRCLE  D=0.559mm                                                         DRAW  Material
D74	CIRCLE  D=0.172mm                                                         DRAW  Material
D75	CIRCLE  D=0.461mm                                                         DRAW  Material
D76	CIRCLE  D=0.473mm                                                         DRAW  Material
D77	CIRCLE  D=0.579mm                                                         DRAW  Material
D78	CIRCLE  D=0.244mm                                                         DRAW  Material
D79	CIRCLE  D=0.035mm                                                         DRAW  Material
D80	CIRCLE  D=0.381mm                                                         FLASH ViaDrill
D81	CIRCLE  D=0.254mm                                                         FLASH ViaDrill
D82	CIRCLE  D=0.762mm                                                         FLASH ComponentDrill
D83	CIRCLE  D=0.889mm                                                         FLASH ComponentDrill
D84	CIRCLE  D=1.524mm                                                         FLASH ComponentDrill
D85	CIRCLE  D=1.016mm                                                         FLASH ComponentDrill
D86	CIRCLE  D=0.813mm                                                         FLASH ComponentDrill

Layer Stackup
-------------
Top Solder Resist        : 0.01mm     Resist
Top Copper               : 0.035mm    Copper
Core                     : 1.6mm      FR4
Bottom Copper            : 0.035mm    Copper
Bottom Solder Resist     : 0.01mm     Resist

[END OF FILE]

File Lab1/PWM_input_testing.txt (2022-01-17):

0.001	0
0.002	12
0.003	0
0.004	0
0.005	0
0.006	0
0.007	0
0.008	0
0.009	0
0.01	0
0.011	0
0.012	0
0.013	0
0.014	0
0.015	0
0.016	0
0.017	0
0.018	0
0.019	0
0.02	0
0.021	0
0.022	0
0.023	0
0.024	0
0.025	0
0.026	0
0.027	0
0.028	0
0.029	0
0.03	0
0.031	0
0.032	0
0.033	0
0.034	0
0.035	0
0.036	0
0.037	0
0.038	0
0.039	0
0.04	0
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

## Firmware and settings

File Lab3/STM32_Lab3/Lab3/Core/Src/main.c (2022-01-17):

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
/* Includes ------------------------------------------------------------------*/
#include "main.h"

TIM_HandleTypeDef htim1;
TIM_HandleTypeDef htim2;
TIM_HandleTypeDef htim3;

UART_HandleTypeDef huart2;
UART_HandleTypeDef huart6;

void SystemClock_Config(void);
static void MX_GPIO_Init(void);
static void MX_USART2_UART_Init(void);
static void MX_USART6_UART_Init(void);
static void MX_TIM1_Init(void);
static void MX_TIM3_Init(void);
static void MX_TIM2_Init(void);
/* USER CODE BEGIN 0 */

/*** GLOBAL VARIABLES ***/

/* Useful LCD Instructions */

uint8_t LCD_InstRcv = 0xFE;
uint8_t LCD_NewLine = 0xC0;
uint8_t LCD_Beginning = 0x80;
uint8_t LCD_Clear = 1;

/* Button Types for User Input */

typedef enum {
	start_e		= 1,
	enter_e		= 2,
	scroll_e	= 4
} button;

button next_valid_button = start_e;

/* Operational Mode Variables */

typedef enum {
	locked_mode_e,
	setup_mode_e,
	run_mode_e,
	choosing_mode_e
} state;

int first_entering_state = 0;
state mode_state = choosing_mode_e;
state current_mode_display = 0;
uint8_t operation_modes[3][5] = {"Lock ", "Setup", "Run  "};

/* Locked Type Modes */

typedef enum {
	locked_closed_e,
	locked_opened_e
} lock_mode;

lock_mode current_locked_display = locked_closed_e;
uint8_t locked_modes[2][10] = {"Close Door", "Open Door "};

/* User Input Parameters */

typedef enum {
	P1_e,
	P2_e,
	P3_e,
	P4_e,
	P5_e
} parameter;

parameter current_parameter = P1_e;
int current_parameter_index = 0;

int p1_p2_values[4] = {8, 2, 4, 6};
int p3_values[4] = {20, 5, 10, 15};
uint32_t p4_p5_values[4] = {40000, 17000, 25000, 30000};

uint8_t p1_p2_display[4][11] = {"8ft Y:Enter", "2ft Y:Enter", "4ft Y:Enter", "6ft Y:Enter"};
uint8_t p3_display[4][13] = {"20sec Y:Enter", "05sec Y:Enter", "10sec Y:Enter", "15sec Y:Enter"};
uint8_t p4_p5_display[4][15] = {"Speed 4 Y:Enter", "Speed 1 Y:Enter", "Speed 2 Y:Enter", "Speed 3 Y:Enter"};

int P1 = 0;
int P2 = 0;
int P3 = 0;
uint32_t P4 = 0;
uint32_t P5 = 0;

/* Misc. Flags */

int collision = 0;
int running = 0;
int door_closed = 0;
int door_opened = 0;

/* Ultrasonic Variables */

typedef enum {
	  not_within_boundaries_e = 0,
	  within_inside_ultrasonic_e = 1,
	  within_outside_ultrasonic_e = 2
} boundary;

boundary object_in_boundaries = not_within_boundaries_e;

int inside_us_rising_edge = 1;
uint32_t inside_us_prev_time = 0;
uint32_t inside_us_curr_time = 0;

int outside_us_rising_edge = 1;
uint32_t outside_us_prev_time = 0;
uint32_t outside_us_curr_time = 0;


/*** HELPER FUNCTION DECLARATIONS ***/


/* @brief Helper function to display strings to LCD
 * @param line1: uint8_t array to display on first line of the LCD
 * @param line1_size: size of line1
 * @param line2: uint8_t array to display on seconds line of the LCD
 * @param line2_size: size of line2
 */

void display_lcd(uint8_t line1[], size_t line1_size, uint8_t line2[], size_t line2_size);

/* @brief Helper function to rotate the motor in forward direction (+ve RPM)
 * @param ch1_limit: int32_t max voltage for the motor driver IN1
 * @param ch1_step: int32_t step size for PWM
 */

void motor_forward(int32_t ch1_limit, int32_t ch1_step);

/* @brief Helper function to rotate the motor in reverse direction (-ve RPM)
 * @param ch2_limit: int32_t max voltage for the motor driver IN2
 * @param ch2_step: int32_t step size for PWM
 */

void motor_reverse(int32_t ch2_limit, int32_t ch2_step);

/* @brief Helper function to turn off the motor
 */

void motor_off();

/* @brief Helper function to calculate microseconds given two clock counters
 * @param previous: uint32_t clock counter value at beginning of measurement
 * @param current: uint32_t clock counter value at end of measurement
 */

uint32_t get_microseconds(uint32_t previous, uint32_t current);

/* @brief Helper function to calculate inches of object from ultrasonic sensor
 * @param time: uint32_t microseconds of active high from ultrasonic
 */

int get_ultrasonic_inches(uint32_t time_us);


/* USER CODE END 0 */

/**
  * @brief  The application entry point.
  * @retval int
  */
int main(void)
{
  /* MCU Configuration--------------------------------------------------------*/

  /* Reset of all peripherals, Initializes the Flash interface and the Systick. */
  HAL_Init();

  /* Configure the system clock */
  SystemClock_Config();

  /* Initialize all configured peripherals */
  MX_GPIO_Init();
  MX_USART2_UART_Init();
  MX_USART6_UART_Init();
  MX_TIM1_Init();
  MX_TIM3_Init();
  MX_TIM2_Init();
  /* USER CODE BEGIN 2 */
  HAL_TIM_Base_Start(&htim1); // start the TIM1 module
  HAL_TIM_PWM_Start(&htim1, TIM_CHANNEL_1); // STart PWM on Channel 1
  HAL_TIM_PWM_Start(&htim1, TIM_CHANNEL_2); // STart PWM on Channel 2
  //HAL_TIM_PWM_Start(&htim1, TIM_CHANNEL_3); // STart PWM on Channel 3
  //HAL_TIM_PWM_Start(&htim1, TIM_CHANNEL_4); // STart PWM on Channel 4


  HAL_TIM_Base_Start_IT(&htim2); //Start the TIM2 module with interrupts enabled
  HAL_TIM_PWM_Start(&htim2, TIM_CHANNEL_1); //Start PWM on CH1
  HAL_TIM_OC_Start_IT(&htim2, TIM_CHANNEL_2); //Start Output Compare on CH2 with interrupts enabled


  HAL_TIM_Base_Start(&htim3);
  HAL_TIM_PWM_Start(&htim1, TIM_CHANNEL_2); // STart PWM on Channel 2
  HAL_TIM_PWM_Start(&htim1, TIM_CHANNEL_3); // STart PWM on Channel 3
  HAL_TIM_PWM_Start(&htim1, TIM_CHANNEL_4); // STart PWM on Channel 4

  /* USER CODE END 2 */

  /* Infinite loop */
  /* USER CODE BEGIN WHILE */

start:
  while (1)
  {

	  /* Collision Flag
	   * Stop everything until collision is over
	   */
	  while (collision) {
		  HAL_GPIO_WritePin(GPIOA, GPIO_PIN_11, GPIO_PIN_SET);
		  HAL_Delay(500);
		  HAL_GPIO_WritePin(GPIOA, GPIO_PIN_11, GPIO_PIN_RESET);
	  }


	  if (running) {


		  HAL_GPIO_WritePin(GPIOC, GPIO_PIN_9, GPIO_PIN_SET);
		  HAL_GPIO_WritePin(GPIOC, GPIO_PIN_11, GPIO_PIN_SET);

		  uint32_t start_time = __HAL_TIM_GetCounter(&htim2);
		  while (__HAL_TIM_GetCounter(&htim2) <= start_time + 10) {}

		  HAL_GPIO_WritePin(GPIOC, GPIO_PIN_9, GPIO_PIN_RESET);
		  HAL_GPIO_WritePin(GPIOC, GPIO_PIN_11, GPIO_PIN_RESET);

		  HAL_Delay(60);

	  }

	  if (object_in_boundaries & (within_outside_ultrasonic_e | within_inside_ultrasonic_e)) {

		  object_in_boundaries = not_within_boundaries_e;

		  motor_reverse (P4, 1000);
		  while (!door_opened) {
			  if (collision) {
				  goto start;
			  }
		  }

		  HAL_Delay(P3 * 1000);

		  motor_forward (P4, 1000);
		  while (!door_closed) {
			  if (collision) {
				  goto start;
			  }
		  }

	  }


    /* USER CODE END WHILE */

    /* USER CODE BEGIN 3 */
  }
  /* USER CODE END 3 */
}

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
/* USER CODE BEGIN 4 */

void HAL_GPIO_EXTI_Callback(uint16_t GPIO_Pin)
{
	if(GPIO_Pin == GPIO_PIN_5) {	// Start Button

		current_parameter = P1_e;
		current_parameter_index = 0;
		running = 0;
		mode_state = choosing_mode_e;
		uint8_t line1[] = "Press Scroll";
		uint8_t line2[] = "To Choose a Mode";
		display_lcd(line1, sizeof(line1), line2, sizeof(line2));
		next_valid_button = scroll_e;

	}
	else if(GPIO_Pin == GPIO_PIN_6 && next_valid_button & enter_e) // Enter Button
    {

		switch(mode_state){

		case choosing_mode_e:

			first_entering_state = 1;
			mode_state = current_mode_display;
			uint8_t line1[] = "Press Enter";
			uint8_t line2[] = "Again To Begin";
			display_lcd(line1, sizeof(line1), line2, sizeof(line2));
			next_valid_button = enter_e;

			break;

		case locked_mode_e:

			if(first_entering_state){

				first_entering_state = 0;
				uint8_t line1[] = "In Locked Mode";
				uint8_t line2[] = "Press Scroll";
				display_lcd(line1, sizeof(line1), line2, sizeof(line2));
				next_valid_button = scroll_e;

			}
			else {

				next_valid_button = start_e;
				if(current_locked_display == locked_closed_e) {
					uint8_t line1[] = "In Locked Mode";
					uint8_t line2[] = "Closing Door";
					display_lcd(line1, sizeof(line1), line2, sizeof(line2));

					motor_forward(17000, 1000);

				}
				else {
					uint8_t line1[] = "In Locked Mode";
					uint8_t line2[] = "Opening Door";
					display_lcd(line1, sizeof(line1), line2, sizeof(line2));

					motor_reverse(17000, 1000);

				}
			}
			break;

		case setup_mode_e:

			if(first_entering_state){

				first_entering_state = 0;
				uint8_t line1[] = "In Setup Mode";
				uint8_t line2[] = "Press Scroll";
				display_lcd(line1, sizeof(line1), line2, sizeof(line2));
				next_valid_button = scroll_e;

			}
			else {

				if(current_parameter == P1_e) {

					P1 = p1_p2_values[current_parameter_index];
					current_parameter = P2_e;
					next_valid_button = scroll_e;

	    			uint8_t line1[] = "P1 Set. Press";
	    			uint8_t line2[] = "scroll to set P2";
					display_lcd(line1, sizeof(line1), line2, sizeof(line2));

				}
				else if(current_parameter == P2_e) {

					P2 = p1_p2_values[current_parameter_index];
					current_parameter = P3_e;
					next_valid_button = scroll_e;

					uint8_t line1[] = "P2 Set. Press";
					uint8_t line2[] = "scroll to set P3";
					display_lcd(line1, sizeof(line1), line2, sizeof(line2));

				}
				else if(current_parameter == P3_e) {

					P3 = p3_values[current_parameter_index];
					current_parameter = P4_e;
					next_valid_button = scroll_e;

					uint8_t line1[] = "P3 Set. Press";
					uint8_t line2[] = "scroll to set P4";
					display_lcd(line1, sizeof(line1), line2, sizeof(line2));

				}
				else if(current_parameter == P4_e) {

					P4 = p4_p5_values[current_parameter_index];
					current_parameter = P5_e;
					next_valid_button = scroll_e;

					uint8_t line1[] = "P4 Set. Press";
					uint8_t line2[] = "scroll to set P5";
					display_lcd(line1, sizeof(line1), line2, sizeof(line2));

				}
				else if(current_parameter == P5_e) {

					P5 = p4_p5_values[current_parameter_index];
					next_valid_button = start_e;

					uint8_t line1[] = "Setup Complete";
					uint8_t line2[] = "Press Start";
					display_lcd(line1, sizeof(line1), line2, sizeof(line2));

				}

				current_parameter_index = 0;

			}

			break;

		case run_mode_e:

			if (!P1 || !P2 || !P3 || !P4 || !P5) {
				uint8_t line1[] = "ERROR:SETUP";
				uint8_t line2[] = "Press START";
				display_lcd(line1, sizeof(line1), line2, sizeof(line2));
				next_valid_button = start_e;
				break;
			}


			running = 1;
			uint8_t line3[] = "In Run Mode";
			uint8_t line4[] = "Exit:Press Start";
			display_lcd(line3, sizeof(line3), line4, sizeof(line4));

			break;


		default:
			break;

		}
    }
    else if(GPIO_Pin == GPIO_PIN_7 && next_valid_button & scroll_e)	// Scroll Button
    {

    	uint8_t line2[] = "Y:Enter N:Start";
    	switch(mode_state){

    	case choosing_mode_e:

    		current_mode_display = (current_mode_display + 1) % 3;
    		display_lcd(operation_modes[current_mode_display], sizeof(operation_modes[current_mode_display]), line2, sizeof(line2));
    		next_valid_button = enter_e | scroll_e;
    		break;

    	case locked_mode_e:

    		current_locked_display = (current_locked_display + 1) % 2;
    		display_lcd(locked_modes[current_locked_display], sizeof(locked_modes[current_locked_display]), line2, sizeof(line2));
    		next_valid_button = enter_e | scroll_e;
    		break;

    	case setup_mode_e:

    		current_parameter_index = (current_parameter_index + 1) % 4;

    		if(current_parameter == P1_e) {

    			uint8_t line1[] = "Setup Mode. P1:";
				display_lcd(line1, sizeof(line1), p1_p2_display[current_parameter_index], sizeof(p1_p2_display[current_parameter_index]));

			}
    		else if(current_parameter == P2_e) {

    			uint8_t line1[] = "Setup Mode. P2:";
				display_lcd(line1, sizeof(line1), p1_p2_display[current_parameter_index], sizeof(p1_p2_display[current_parameter_index]));

			}
    		else if(current_parameter == P3_e) {

    			uint8_t line1[] = "Setup Mode. P4:";
				display_lcd(line1, sizeof(line1), p3_display[current_parameter_index], sizeof(p3_display[current_parameter_index]));

			}
    		else if(current_parameter == P4_e) {

				uint8_t line1[] = "Setup Mode. P4:";
				display_lcd(line1, sizeof(line1), p4_p5_display[current_parameter_index], sizeof(p4_p5_display[current_parameter_index]));

			}
    		else if(current_parameter == P5_e) {

    			uint8_t line1[] = "Setup Mode. P5:";
				display_lcd(line1, sizeof(line1), p4_p5_display[current_parameter_index], sizeof(p4_p5_display[current_parameter_index]));

			}

			next_valid_button = enter_e | scroll_e;

    		break;

    	case run_mode_e:
    		break;

    	default:
    		break;

    	}

    }
    else if(GPIO_Pin == GPIO_PIN_0)	// Open Limit Switch
	{
    	door_opened = 1;
    	motor_forward(20000, 1000);
    	motor_off();
	}
    else if(GPIO_Pin == GPIO_PIN_1)	// Close Limit Switch
	{
    	door_closed = 1;
    	motor_reverse(20000, 1000);
		motor_off();
	}
    else if(GPIO_Pin == GPIO_PIN_9)	// Inside Ultrasonic Interrupt
	{

    	if (inside_us_rising_edge) {

    		inside_us_rising_edge = 0;
    		inside_us_prev_time = __HAL_TIM_GetCounter(&htim2);
    		HAL_GPIO_WritePin(GPIOA, GPIO_PIN_9, GPIO_PIN_RESET);

    	}
    	else {

    		inside_us_rising_edge = 1;
    		inside_us_curr_time = __HAL_TIM_GetCounter(&htim2);
    		uint32_t time = get_microseconds(inside_us_prev_time, inside_us_curr_time);

    		if (get_ultrasonic_inches(time) <= P2 * 12) {

    			object_in_boundaries |= within_inside_ultrasonic_e;
    			HAL_GPIO_WritePin(GPIOA, GPIO_PIN_9, GPIO_PIN_SET);

    		}

    	}

	}
    else if(GPIO_Pin == GPIO_PIN_10)	// Outside Ultrasonic Interrupt
	{

		if (outside_us_rising_edge) {

			outside_us_rising_edge = 0;
			outside_us_prev_time = __HAL_TIM_GetCounter(&htim2);
			HAL_GPIO_WritePin(GPIOA, GPIO_PIN_8, GPIO_PIN_RESET);

		}
		else {

			outside_us_rising_edge = 1;
			outside_us_curr_time = __HAL_TIM_GetCounter(&htim2);
			uint32_t time = get_microseconds(outside_us_prev_time, outside_us_curr_time);

			if (get_ultrasonic_inches(time) <= P3 * 12) {

				object_in_boundaries |= within_outside_ultrasonic_e;
				HAL_GPIO_WritePin(GPIOA, GPIO_PIN_8, GPIO_PIN_SET);

			}

		}

	}
    else if(GPIO_Pin == GPIO_PIN_2)	// Collision Switch
	{

    	if (!collision) {

    		collision = 1;
    		motor_off();

    	}
    	else {

    		collision = 0;
    		motor_forward (17000, 1000);

    	}

	}
    else if(GPIO_Pin == GPIO_PIN_8)	// Q1 Signal
	{
		HAL_GPIO_TogglePin(GPIOA, GPIO_PIN_10);
	}
    else if(GPIO_Pin == GPIO_PIN_12)	// IDX Signal
    {
    	//HAL_GPIO_TogglePin(GPIOA, GPIO_PIN_10);
    }
}


/*** HELPER FUNCTION DEFINITIONS ***/

/* @brief Helper function to display strings to LCD
 * @param line1: uint8_t array to display on first line of the LCD
 * @param line1_size: size of line1
 * @param line2: uint8_t array to display on seconds line of the LCD
 * @param line2_size: size of line2
 */

void display_lcd(uint8_t line1[], size_t line1_size, uint8_t line2[], size_t line2_size) {

	HAL_UART_Transmit(&huart6, &LCD_InstRcv, 1, 1000);
	HAL_UART_Transmit(&huart6, &LCD_Clear, 1, 1000);


	if (line1 != NULL && line1_size != 0){
		HAL_UART_Transmit(&huart6, &LCD_InstRcv, 1, 1000);
		HAL_UART_Transmit(&huart6, &LCD_Beginning, 1, 1000);
		HAL_UART_Transmit(&huart6, line1, line1_size, 1000);
	}

	if (line2 != NULL && line2_size != 0){
		HAL_UART_Transmit(&huart6, &LCD_InstRcv, 1, 1000);
		HAL_UART_Transmit(&huart6, &LCD_NewLine, 1, 1000);
		HAL_UART_Transmit(&huart6, line2, line2_size, 1000);
	}

}

/* @brief Helper function to rotate the motor in forward direction (+ve RPM)
 * @param ch1_limit: int32_t max voltage for the motor driver IN1
 * @param ch1_step: int32_t step size for PWM
 */

void motor_forward(int32_t ch1_limit, int32_t ch1_step) {

	door_opened = 0;
	int32_t CH1_DC = 0;

	/* Move the Motor Forward */
	while (CH1_DC < ch1_limit) {
		TIM1->CCR1 = CH1_DC;
		TIM1->CCR2 = 0;
		CH1_DC += 1000;
	}
}

/* @brief Helper function to rotate the motor in reverse direction (-ve RPM)
 * @param ch2_limit: int32_t max voltage for the motor driver IN2
 * @param ch2_step: int32_t step size for PWM
 */

void motor_reverse(int32_t ch2_limit, int32_t ch2_step) {

	door_closed = 0;
	int32_t CH2_DC = 0;

	/* Move the Motor Backward */
	while (CH2_DC < ch2_limit) {
		TIM1->CCR1 = 0;
		TIM1->CCR2 = CH2_DC;
		CH2_DC += ch2_step;
	}
}

/* @brief Helper function to turn off the motor
 */

void motor_off() {

	TIM1->CCR1 = 0;
	TIM1->CCR2 = 0;

}


/* @brief Helper function to calculate microseconds given two clock counters
 * @param previous: uint32_t clock counter value at beginning of measurement
 * @param current: uint32_t clock counter value at end of measurement
 */

uint32_t get_microseconds(uint32_t previous, uint32_t current) {

	return previous < current ? current - previous : (100000 - previous) + current;

}

/* @brief Helper function to calculate inches of object from ultrasonic sensor
 * @param time: uint32_t microseconds of active high from ultrasonic
 */

int get_ultrasonic_inches(uint32_t time_us) {

	return time_us / 148;

}

/* USER CODE END 4 */
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


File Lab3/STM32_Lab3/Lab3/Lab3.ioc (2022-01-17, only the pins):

Mcu.UserName=STM32F401RETx
PC10.Signal=GPXTI10
PA14.GPIO_Label=TCK
PB13.Signal=TIM1_CH1N
PB6.Signal=GPXTI6
PC7.Signal=USART6_RX
PC13-ANTI_TAMP.Signal=GPXTI13
PB7.Signal=GPXTI7
PA8.Signal=GPIO_Output
PB9.Signal=GPXTI9
PA6.Signal=S_TIM3_CH1
PA2.GPIO_Label=USART_TX
PA10.Signal=GPIO_Output
PA15.Signal=S_TIM2_CH1_ETR
PA3.Signal=USART2_RX
PB3.GPIO_Label=SWO
PC13-ANTI_TAMP.GPIO_Label=B1 [Blue PushButton]
PC11.Signal=GPIO_Output
PC2.Signal=GPXTI2
PC6.Signal=USART6_TX
PC0.Signal=GPXTI0
PC14-OSC32_IN.Signal=RCC_OSC32_IN
PA13.Signal=SYS_JTMS-SWDIO
PA9.Signal=GPIO_Output
PC15-OSC32_OUT.Signal=RCC_OSC32_OUT
PB14.Signal=TIM1_CH2N
PA5.Signal=GPIO_Output
PA2.Signal=USART2_TX
PA13.GPIO_Label=TMS
PB3.Signal=SYS_JTDO-SWO
PB5.Signal=GPXTI5
PA5.GPIO_Label=LD2 [Green Led]
PA11.Signal=GPIO_Output
PA14.Signal=SYS_JTCK-SWCLK
PB8.Signal=GPXTI8
PC9.Signal=GPIO_Output
PC1.Signal=GPXTI1
PA3.GPIO_Label=USART_RX

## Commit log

2022-01-17 Add project files
    [ECE298_Lab4_pickandplace.csv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]
2022-01-17 Clean up repo
    [ECE298_Lab4_pickandplace.csv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]

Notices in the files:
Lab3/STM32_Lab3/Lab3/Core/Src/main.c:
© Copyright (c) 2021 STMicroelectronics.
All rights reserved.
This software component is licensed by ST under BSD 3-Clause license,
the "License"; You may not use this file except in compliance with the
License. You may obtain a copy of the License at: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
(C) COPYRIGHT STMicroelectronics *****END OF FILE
